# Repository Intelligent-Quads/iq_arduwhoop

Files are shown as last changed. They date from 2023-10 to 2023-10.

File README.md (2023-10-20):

# IQ Arduwhoop

This project holds parameters, scripts and other information about my arduwhoop build. The goal of this project was to make a tiny whoop drone that was capable of running Ardupilot. This drone consists of the flywoo GN745 AIO ESC FC board with the GM8 GPS and the MRO SIK telemetry radio. The drone is powered by a 2s 420mah battery. The total weight of the drone with battery is 76g. If you would like to build your own, the parts list can be found at the link below. 

https://docs.google.com/spreadsheets/d/1IXLM4TMvut4r6jN9-gEEboaGNLur6-ZLpiZj0F0QWQA/edit?usp=sharing

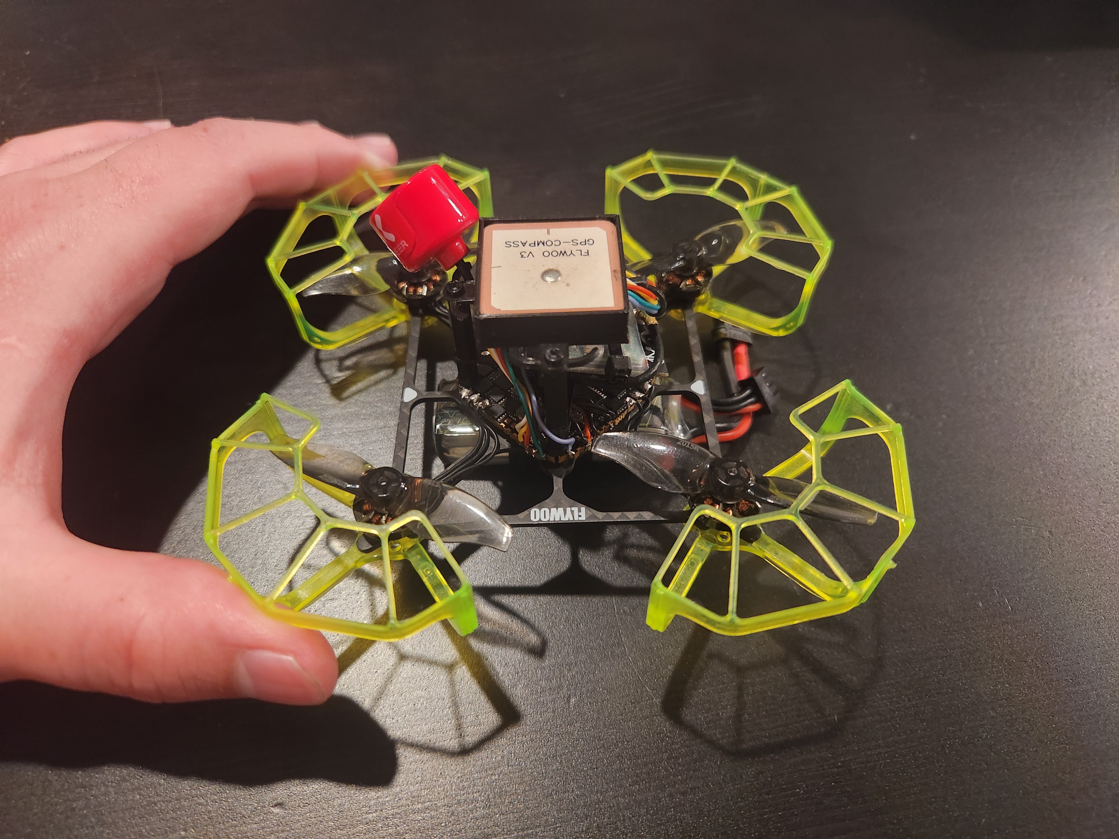
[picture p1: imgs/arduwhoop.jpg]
whoop with hand


## 3D Printed Parts

The 3D printed parts for this drone can be found in the `stls` folder. 

## Wiring 

GN745

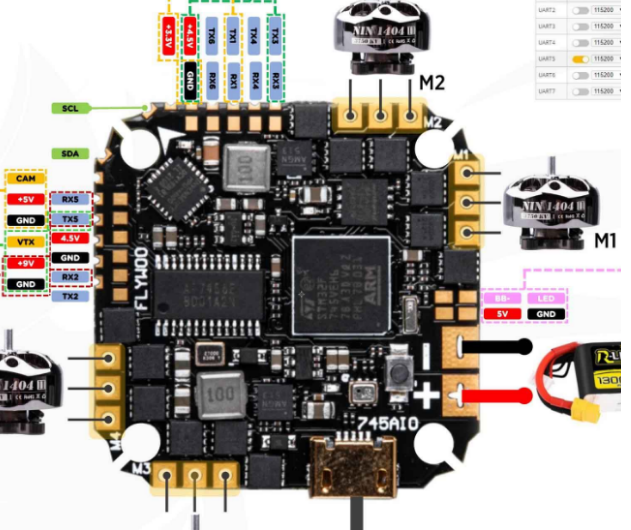
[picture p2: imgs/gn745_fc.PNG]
gn745


### GPS 
| GPS |  FC  |
|-----|---|
| T | RX6  |
| R | TX6  |
| G | Gnd  |
| V | 4.5V |
| C | SCL  |
| D | SDA  |

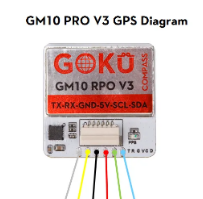
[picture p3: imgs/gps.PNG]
gps


### Telemetry Radio

| RADIO |  FC  |
|---|---|
| VCC | 4.5V |
| RX | TX5  |
| TX | RX5  |
| RTS | RX2  |
| CTS | TX2  |
| GND | GND  |

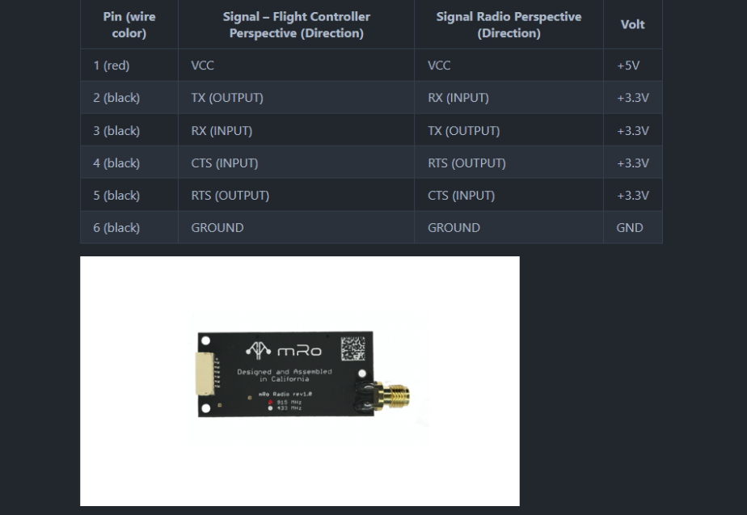
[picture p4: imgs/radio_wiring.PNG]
Radio Wiring


## Firmware Setup

### Flashing the firmware

I followed this guide to flash the firmware onto the FC the first time since the gn745 does not come with ardupilot preinstalled so you won't be able to flash it with mission planner the first time. 

https://ardupilot.org/copter/docs/common-loading-firmware-onto-chibios-only-boards.html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

### Configuring the firmware 

Upload the Parameter file `params/arduwhoop_tune_no_calibration.params`. To see an explaination of the parameters, see [this section](#parameter-explanation) below.

Be sure to do the following calibrations before flying.

- Gyro
- accelerometer
- compass
- ESC calibration

### Motor Spin Direction

More than likely there will be a motor or 2 that will need it's spin direction reversed. You will need to use the blheli configurator to do this. this link describes how to do this.

https://ardupilot.org/copter/docs/common-blheli32-passthru.html#pass-through-support

## Parameter Explanation

- ATC - Attitude and rate controller gains and parameters
- BATT_FS_CRT_ACT 1 - land when battery is critically low
- BATT_FS_LOW_ACT 2 - RTL when battery is low
- BATT_LOW_VOLT	7.19 - voltage at which battery is considered low
- FRAME_CLASS	1 - quadcopter
- FRAME_TYPE	12 - BetaflightX
- FS_GCS_ENABLE	1 - enable failsafe when GCS is lost
- MOT_SPIN_ARM	0.15 - minimum motor spin speed when armed
- MOT_SPOOL_TIME	1.2 - time to spool up motors when armed
- PILOT_TKOFF_ALT	1 - minimum commandable altitude from GCS
- PSC - position control gains and parameters
- RTL_ALT	600 - altitude to return to when RTL is triggered
- RTL_LOIT_TIME	1000 - time to loiter at RTL_ALT before landing
- SERIAL5_PROTOCOL	2 - mavlink telemetry for sik radio
- servoX_function - motor mapping 
- SERVO_BLH_AUTO 1 - enable blheli passthrough
- WPNAV_SPEED	400 - maximum speed in cm/s
- WPNAV_SPEED_UP	200 - maximum speed in cm/s when ascending

## Links 

gn745 ardupilot docs
- https://ardupilot.org/copter/docs/common-flywoo-f745.html

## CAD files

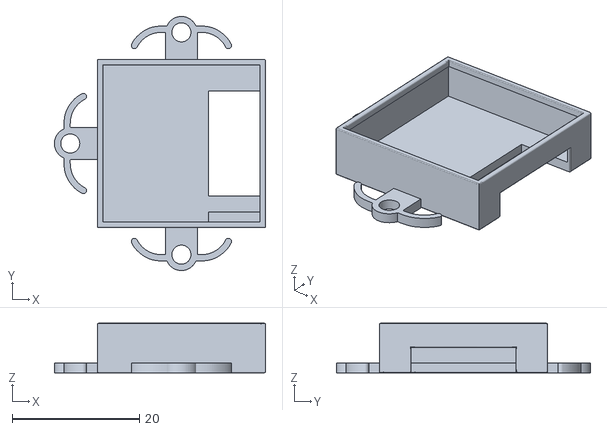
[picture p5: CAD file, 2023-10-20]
stls/gm10_holder v5.stl
33.2 x 40.0 x 7.80

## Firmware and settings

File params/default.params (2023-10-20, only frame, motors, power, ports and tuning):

1	1	ATC_ANGLE_BOOST	1	2
1	1	ATC_ANG_LIM_TC	1.000000000000000000	9
1	1	ATC_ANG_PIT_P	4.500000000000000000	9
1	1	ATC_ANG_RLL_P	4.500000000000000000	9
1	1	ATC_ANG_YAW_P	4.500000000000000000	9
1	1	ATC_RATE_FF_ENAB	1	2
1	1	ATC_RATE_P_MAX	0.000000000000000000	9
1	1	ATC_RATE_R_MAX	0.000000000000000000	9
1	1	ATC_RATE_Y_MAX	0.000000000000000000	9
1	1	ATC_RAT_PIT_D	0.003599999938160181	9
1	1	ATC_RAT_PIT_FF	0.000000000000000000	9
1	1	ATC_RAT_PIT_FLTD	20.000000000000000000	9
1	1	ATC_RAT_PIT_FLTE	0.000000000000000000	9
1	1	ATC_RAT_PIT_FLTT	20.000000000000000000	9
1	1	ATC_RAT_PIT_I	0.135000005364418030	9
1	1	ATC_RAT_PIT_IMAX	0.500000000000000000	9
1	1	ATC_RAT_PIT_P	0.135000005364418030	9
1	1	ATC_RAT_PIT_SMAX	0.000000000000000000	9
1	1	ATC_RAT_RLL_D	0.003599999938160181	9
1	1	ATC_RAT_RLL_FF	0.000000000000000000	9
1	1	ATC_RAT_RLL_FLTD	20.000000000000000000	9
1	1	ATC_RAT_RLL_FLTE	0.000000000000000000	9
1	1	ATC_RAT_RLL_FLTT	20.000000000000000000	9
1	1	ATC_RAT_RLL_I	0.135000005364418030	9
1	1	ATC_RAT_RLL_IMAX	0.500000000000000000	9
1	1	ATC_RAT_RLL_P	0.135000005364418030	9
1	1	ATC_RAT_RLL_SMAX	0.000000000000000000	9
1	1	ATC_RAT_YAW_D	0.000000000000000000	9
1	1	ATC_RAT_YAW_FF	0.000000000000000000	9
1	1	ATC_RAT_YAW_FLTD	0.000000000000000000	9
1	1	ATC_RAT_YAW_FLTE	2.500000000000000000	9
1	1	ATC_RAT_YAW_FLTT	20.000000000000000000	9
1	1	ATC_RAT_YAW_I	0.017999999225139618	9
1	1	ATC_RAT_YAW_IMAX	0.500000000000000000	9
1	1	ATC_RAT_YAW_P	0.180000007152557373	9
1	1	ATC_RAT_YAW_SMAX	0.000000000000000000	9
1	1	BATT2_MONITOR	0	2
1	1	BATT3_MONITOR	0	2
1	1	BATT4_MONITOR	0	2
1	1	BATT5_MONITOR	0	2
1	1	BATT6_MONITOR	0	2
1	1	BATT7_MONITOR	0	2
1	1	BATT8_MONITOR	0	2
1	1	BATT9_MONITOR	0	2
1	1	BATT_AMP_OFFSET	0.000000000000000000	9
1	1	BATT_AMP_PERVLT	28.500000000000000000	9
1	1	BATT_ARM_MAH	0	6
1	1	BATT_ARM_VOLT	0.000000000000000000	9
1	1	BATT_CAPACITY	3300	6
1	1	BATT_CRT_MAH	0.000000000000000000	9
1	1	BATT_CRT_VOLT	0.000000000000000000	9
1	1	BATT_CURR_PIN	12	2
1	1	BATT_FS_CRT_ACT	0	2
1	1	BATT_FS_LOW_ACT	0	2
1	1	BATT_FS_VOLTSRC	0	2
1	1	BATT_LOW_MAH	0.000000000000000000	9
1	1	BATT_LOW_TIMER	10	2
1	1	BATT_LOW_VOLT	10.500000000000000000	9
1	1	BATT_MONITOR	4	2
1	1	BATT_OPTIONS	0	6
1	1	BATT_SERIAL_NUM	-1	6
1	1	BATT_VLT_OFFSET	0.000000000000000000	9
1	1	BATT_VOLT_MULT	10.899999618530273438	9
1	1	BATT_VOLT_PIN	13	2
1	1	FLTMODE1	0	2
1	1	FLTMODE2	0	2
1	1	FLTMODE3	0	2
1	1	FLTMODE4	0	2
1	1	FLTMODE5	0	2
1	1	FLTMODE6	0	2
1	1	FLTMODE_CH	5	2
1	1	FRAME_CLASS	0	2
1	1	FRAME_TYPE	1	2
1	1	INS_GYRO_FILTER	20	4
1	1	INS_HNTCH_ENABLE	0	2
1	1	MOT_BAT_CURR_MAX	0.000000000000000000	9
1	1	MOT_BAT_CURR_TC	5.000000000000000000	9
1	1	MOT_BAT_IDX	0	2
1	1	MOT_BAT_VOLT_MAX	0.000000000000000000	9
1	1	MOT_BAT_VOLT_MIN	0.000000000000000000	9
1	1	MOT_BOOST_SCALE	0.000000000000000000	9
1	1	MOT_HOVER_LEARN	2	2
1	1	MOT_PWM_MAX	2000	4
1	1	MOT_PWM_MIN	1000	4
1	1	MOT_PWM_TYPE	0	2
1	1	MOT_SAFE_DISARM	0	2
1	1	MOT_SAFE_TIME	1.000000000000000000	9
1	1	MOT_SLEW_DN_TIME	0.000000000000000000	9
1	1	MOT_SLEW_UP_TIME	0.000000000000000000	9
1	1	MOT_SPIN_ARM	0.100000001490116119	9
1	1	MOT_SPIN_MAX	0.949999988079071045	9
1	1	MOT_SPIN_MIN	0.150000005960464478	9
1	1	MOT_SPOOL_TIME	0.500000000000000000	9
1	1	MOT_THST_EXPO	0.649999976158142090	9
1	1	MOT_THST_HOVER	0.349999994039535522	9
1	1	MOT_YAW_HEADROOM	200	4
1	1	SERIAL0_BAUD	115	6
1	1	SERIAL0_PROTOCOL	2	2
1	1	SERIAL1_BAUD	57	6
1	1	SERIAL1_OPTIONS	0	4
1	1	SERIAL1_PROTOCOL	2	2
1	1	SERIAL2_BAUD	57	6
1	1	SERIAL2_OPTIONS	0	4
1	1	SERIAL2_PROTOCOL	2	2
1	1	SERIAL3_BAUD	38	6
1	1	SERIAL3_OPTIONS	0	4
1	1	SERIAL3_PROTOCOL	23	2
1	1	SERIAL4_BAUD	38	6
1	1	SERIAL4_OPTIONS	0	4
1	1	SERIAL4_PROTOCOL	-1	2
1	1	SERIAL5_BAUD	57	6
1	1	SERIAL5_OPTIONS	0	4
1	1	SERIAL5_PROTOCOL	-1	2
1	1	SERIAL6_BAUD	57	6
1	1	SERIAL6_OPTIONS	0	4
1	1	SERIAL6_PROTOCOL	5	2
1	1	SERIAL7_BAUD	57	6
1	1	SERIAL7_OPTIONS	0	4
1	1	SERIAL7_PROTOCOL	-1	2
1	1	SERVO1_FUNCTION	0	4
1	1	SERVO1_MAX	1900	4
1	1	SERVO1_MIN	1100	4
1	1	SERVO1_REVERSED	0	2
1	1	SERVO1_TRIM	1500	4
1	1	SERVO2_FUNCTION	0	4
1	1	SERVO2_MAX	1900	4
1	1	SERVO2_MIN	1100	4
1	1	SERVO2_REVERSED	0	2
1	1	SERVO2_TRIM	1500	4
1	1	SERVO3_FUNCTION	0	4
1	1	SERVO3_MAX	1900	4
1	1	SERVO3_MIN	1100	4
1	1	SERVO3_REVERSED	0	2
1	1	SERVO3_TRIM	1500	4
1	1	SERVO4_FUNCTION	0	4
1	1	SERVO4_MAX	1900	4
1	1	SERVO4_MIN	1100	4
1	1	SERVO4_REVERSED	0	2
1	1	SERVO4_TRIM	1500	4
1	1	SERVO5_FUNCTION	0	4
1	1	SERVO5_MAX	1900	4
1	1	SERVO5_MIN	1100	4
1	1	SERVO5_REVERSED	0	2
1	1	SERVO5_TRIM	1500	4
1	1	SERVO6_FUNCTION	0	4
1	1	SERVO6_MAX	1900	4
1	1	SERVO6_MIN	1100	4
1	1	SERVO6_REVERSED	0	2
1	1	SERVO6_TRIM	1500	4
1	1	SERVO7_FUNCTION	0	4
1	1	SERVO7_MAX	1900	4
1	1	SERVO7_MIN	1100	4
1	1	SERVO7_REVERSED	0	2
1	1	SERVO7_TRIM	1500	4
1	1	SERVO8_FUNCTION	0	4
1	1	SERVO8_MAX	1900	4
1	1	SERVO8_MIN	1100	4
1	1	SERVO8_REVERSED	0	2
1	1	SERVO8_TRIM	1500	4
1	1	SERVO9_FUNCTION	120	4
1	1	SERVO9_MAX	1900	4
1	1	SERVO9_MIN	1100	4
1	1	SERVO9_REVERSED	0	2
1	1	SERVO9_TRIM	1500	4

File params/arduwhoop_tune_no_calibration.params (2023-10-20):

1	1	ATC_ACCEL_P_MAX	207000.000000000000000000	9
1	1	ATC_ACCEL_R_MAX	207000.000000000000000000	9
1	1	ATC_ACCEL_Y_MAX	34200.000000000000000000	9
1	1	ATC_ANGLE_BOOST	1	2
1	1	ATC_ANG_LIM_TC	1.000000000000000000	9
1	1	ATC_ANG_PIT_P	4.000000000000000000	9
1	1	ATC_ANG_RLL_P	4.000000000000000000	9
1	1	ATC_ANG_YAW_P	4.000000000000000000	9
1	1	ATC_INPUT_TC	0.009999999776482582	9
1	1	ATC_RATE_FF_ENAB	1	2
1	1	ATC_RATE_P_MAX	0.000000000000000000	9
1	1	ATC_RATE_R_MAX	0.000000000000000000	9
1	1	ATC_RATE_Y_MAX	0.000000000000000000	9
1	1	ATC_RAT_PIT_D	0.003599999938160181	9
1	1	ATC_RAT_PIT_FF	0.000000000000000000	9
1	1	ATC_RAT_PIT_FLTD	81.000000000000000000	9
1	1	ATC_RAT_PIT_FLTE	0.000000000000000000	9
1	1	ATC_RAT_PIT_FLTT	81.000000000000000000	9
1	1	ATC_RAT_PIT_I	0.079999998211860657	9
1	1	ATC_RAT_PIT_IMAX	0.500000000000000000	9
1	1	ATC_RAT_PIT_P	0.079999998211860657	9
1	1	ATC_RAT_PIT_SMAX	0.000000000000000000	9
1	1	ATC_RAT_RLL_D	0.003599999938160181	9
1	1	ATC_RAT_RLL_FF	0.000000000000000000	9
1	1	ATC_RAT_RLL_FLTD	81.000000000000000000	9
1	1	ATC_RAT_RLL_FLTE	0.000000000000000000	9
1	1	ATC_RAT_RLL_FLTT	81.000000000000000000	9
1	1	ATC_RAT_RLL_I	0.079999998211860657	9
1	1	ATC_RAT_RLL_IMAX	0.500000000000000000	9
1	1	ATC_RAT_RLL_P	0.079999998211860657	9
1	1	ATC_RAT_RLL_SMAX	0.000000000000000000	9
1	1	ATC_RAT_YAW_D	0.000000000000000000	9
1	1	ATC_RAT_YAW_FF	0.000000000000000000	9
1	1	ATC_RAT_YAW_FLTD	0.000000000000000000	9
1	1	ATC_RAT_YAW_FLTE	2.000000000000000000	9
1	1	ATC_RAT_YAW_FLTT	81.000000000000000000	9
1	1	ATC_RAT_YAW_I	0.017999999225139618	9
1	1	ATC_RAT_YAW_IMAX	0.500000000000000000	9
1	1	ATC_RAT_YAW_P	0.180000007152557373	9
1	1	ATC_RAT_YAW_SMAX	0.000000000000000000	9
1	1	ATC_SLEW_YAW	6000.000000000000000000	9
1	1	ATC_THR_G_BOOST	0.000000000000000000	9
1	1	ATC_THR_MIX_MAN	0.100000001490116119	9
1	1	ATC_THR_MIX_MAX	0.500000000000000000	9
1	1	ATC_THR_MIX_MIN	0.100000001490116119	9
1	1	BATT_FS_CRT_ACT	1	2
1	1	BATT_FS_LOW_ACT	2	2
1	1	BATT_LOW_VOLT	7.199999809265136719	9
1	1	FRAME_CLASS	1	2
1	1	FRAME_TYPE	12	2
1	1	FS_GCS_ENABLE	1	2
1	1	MOT_SPIN_ARM	0.150000005960464478	9
1	1	MOT_SPOOL_TIME	1.200000047683715820	9
1	1	PILOT_TKOFF_ALT	1.000000000000000000	9
1	1	PSC_ACCZ_I	0.680000007152557373	9
1	1	PSC_ACCZ_P	0.340000003576278687	9
1	1	RTL_ALT	600	6
1	1	RTL_LOIT_TIME	1000	6
1	1	SERIAL5_PROTOCOL	2	2
1	1	SERVO1_FUNCTION	33	4
1	1	SERVO2_FUNCTION	34	4
1	1	SERVO3_FUNCTION	35	4
1	1	SERVO4_FUNCTION	36	4
1	1	SERVO_BLH_AUTO	1	2
1	1	WPNAV_SPEED	400.000000000000000000	9
1	1	WPNAV_SPEED_UP	200.000000000000000000	9

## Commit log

2023-09-07 safety improvements
    [arduwhoop.params]
2023-09-08 flight params 9-7-2023
    [arduwhoop.params]
2023-09-09 6pm flight
    [arduwhoop.params]
2023-10-20 updated params and instructions
    [arduwhoop_tune_no_calibration.params, default.params, gm10_holder v5.stl]
